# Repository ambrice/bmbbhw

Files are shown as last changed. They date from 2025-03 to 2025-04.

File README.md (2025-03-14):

# Big Mouth Billy Bass Master Control Program

This is the hardware design for the Big Mouth Billy Bass controller.  The current
software (zephyr version) runs on a group of 6 adafruit boards with a lot of
wires running between them.  So this is my first hardware design attempt, to use
the adafruit boards as a reference and compile them into one board.

The adafruit schematics are available under EAGLE which is a dead-end program, so
using KiCad 8 to design the board.  Started with brand-new KiCad 9, but it was
suggested that KiCad 8 would be more stable and have less potential issues with
manufacturing, Osh Park for example accepts KiCad 8 board files directly but not
KiCad 9 yet.

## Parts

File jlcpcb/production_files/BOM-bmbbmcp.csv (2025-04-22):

Comment | Designator | Footprint | LCSC | Quantity
220pF | C8,C9 | C_0805_2012Metric | C107145 | 2
DRV8835DSSR | U4 | DSS0012A | C129328 | 1
MBR120 | D1,D2 | D_SOD-123 | C130880 | 2
USB_OTG | J1 | USB_Micro-AB_Molex_47590-0001 | C136001 | 1
0.1uF | C11,C2,C5 | C_0603_1608Metric | C14663 | 3
10uF | C1,C10,C6,C7 | C_0805_2012Metric | C15850 | 4
22pF | C3,C4 | C_0603_1608Metric | C1653 | 2
22 | R2,R3 | R_0603_1608Metric | C23345 | 2
10k | R1 | R_0603_1608Metric | C25804 | 1
FerriteBead | FB1,FB2 | L_0805_2012Metric | C442498 | 2
AP2112K-3.3 | U2 | SOT-23-5 | C51118 | 1
MDBT50Q-P1MV2 | U1 | Raytac_MDBT50Q | C5119772 | 1
Micro_SD_Card | J4 | microSD_HC_Molex_104031-0811 | C585350 | 1
32.768 | Y1 | Crystal_SMD_MicroCrystal_CC7V-T1A-2Pin_3.2x1.5mm | C620155 | 1
MAX98357A | U3 | TQFN-16-1EP_3x3mm_P0.5mm_EP1.23x1.23mm | C910544 | 1
KMR231GLFS | S1,S2 | SW4SMD_63X161LS | C99271 | 2

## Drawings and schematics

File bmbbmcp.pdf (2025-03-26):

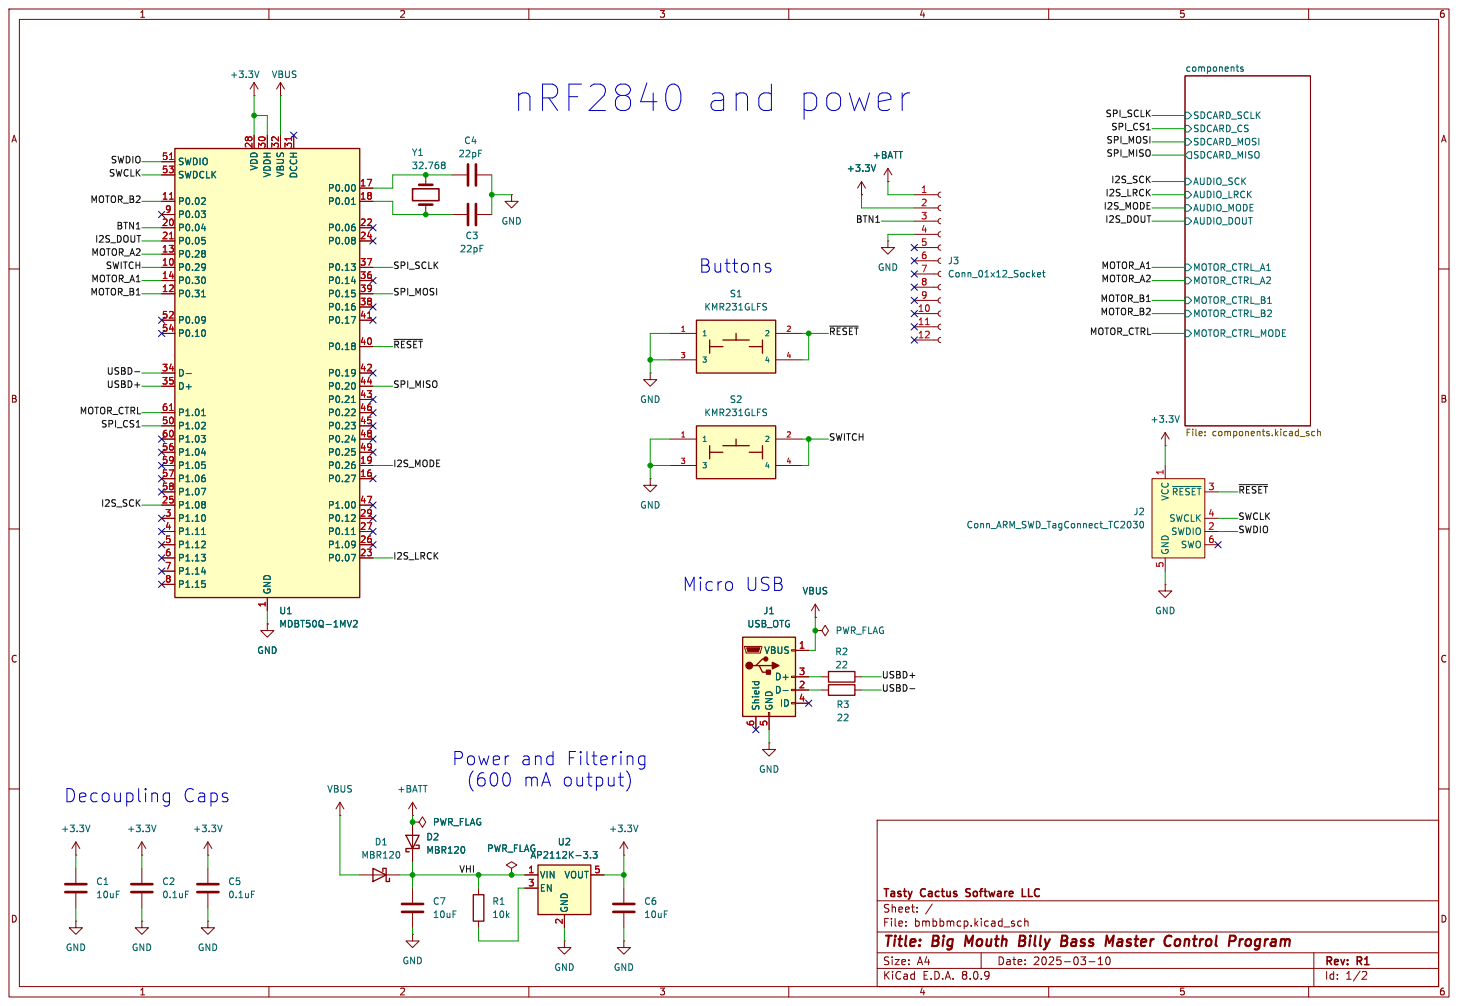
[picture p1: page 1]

1 P0.29 10 P0.02 11 P0.31 12 P0.28 13 P0.30 14 P0.27 16 P0.00 17 P0.01 18 P0.26 19 P0.04 20 P0.05 21 P0.06 22 P0.07 23 P0.08 24 P1.08 25 P1.09 26 P0.11 27 VDD 28 P0.12 29 P1.10 3 VDDH 30 DCCH 31 VBUS 32 D- 34 D+ 35 P0.14 36 P0.13 37 P0.16 38 P0.15 39 P1.11 4 P0.18 40 P0.17 41 P0.19 42 P0.21 43 P0.20 44 P0.23 45 P0.22 46 P1.00 47 P0.24 48 P0.25 49 P1.12 5 P1.02 50 SWDIO 51 P0.09 52 SWDCLK 53 P0.10 54 P1.04 56 P1.06 57 P1.07 58 P1.05 59 P1.13 6 P1.03 60 P1.01 61 P1.14 7 P1.15 8 P0.03 9 U1 MDBT50Q-1MV2 C1
SWDIO
SWCLK

1 P0.29 10 P0.02 11 P0.31 12 P0.28 13 P0.30 14 P0.27 16 P0.00 17 P0.01 18 P0.26 19 P0.04 20 P0.05 21 P0.06 22 P0.07 23 P0.08 24 P1.08 25 P1.09 26 P0.11 27 VDD 28 P0.12 29 P1.10 3 VDDH 30 DCCH 31 VBUS 32 D- 34 D+ 35 P0.14 36 P0.13 37 P0.16 38 P0.15 39 P1.11 4 P0.18 40 P0.17 41 P0.19 42 P0.21 43 P0.20 44 P0.23 45 P0.22 46 P1.00 47 P0.24 48 P0.25 49 P1.12 5 P1.02 50 SWDIO 51 P0.09 52 SWDCLK 53 P0.10 54 P1.04 56 P1.06 57 P1.07 58 P1.05 59 P1.13 6 P1.03 60 P1.01 61 P1.14 7 P1.15 8 P0.03 9 VBUS

1 SWDIO 2 ~{RESET}3 SWCLK 4 GND

Id: 1/2 Title: Big Mouth Billy Bass Master Control Program

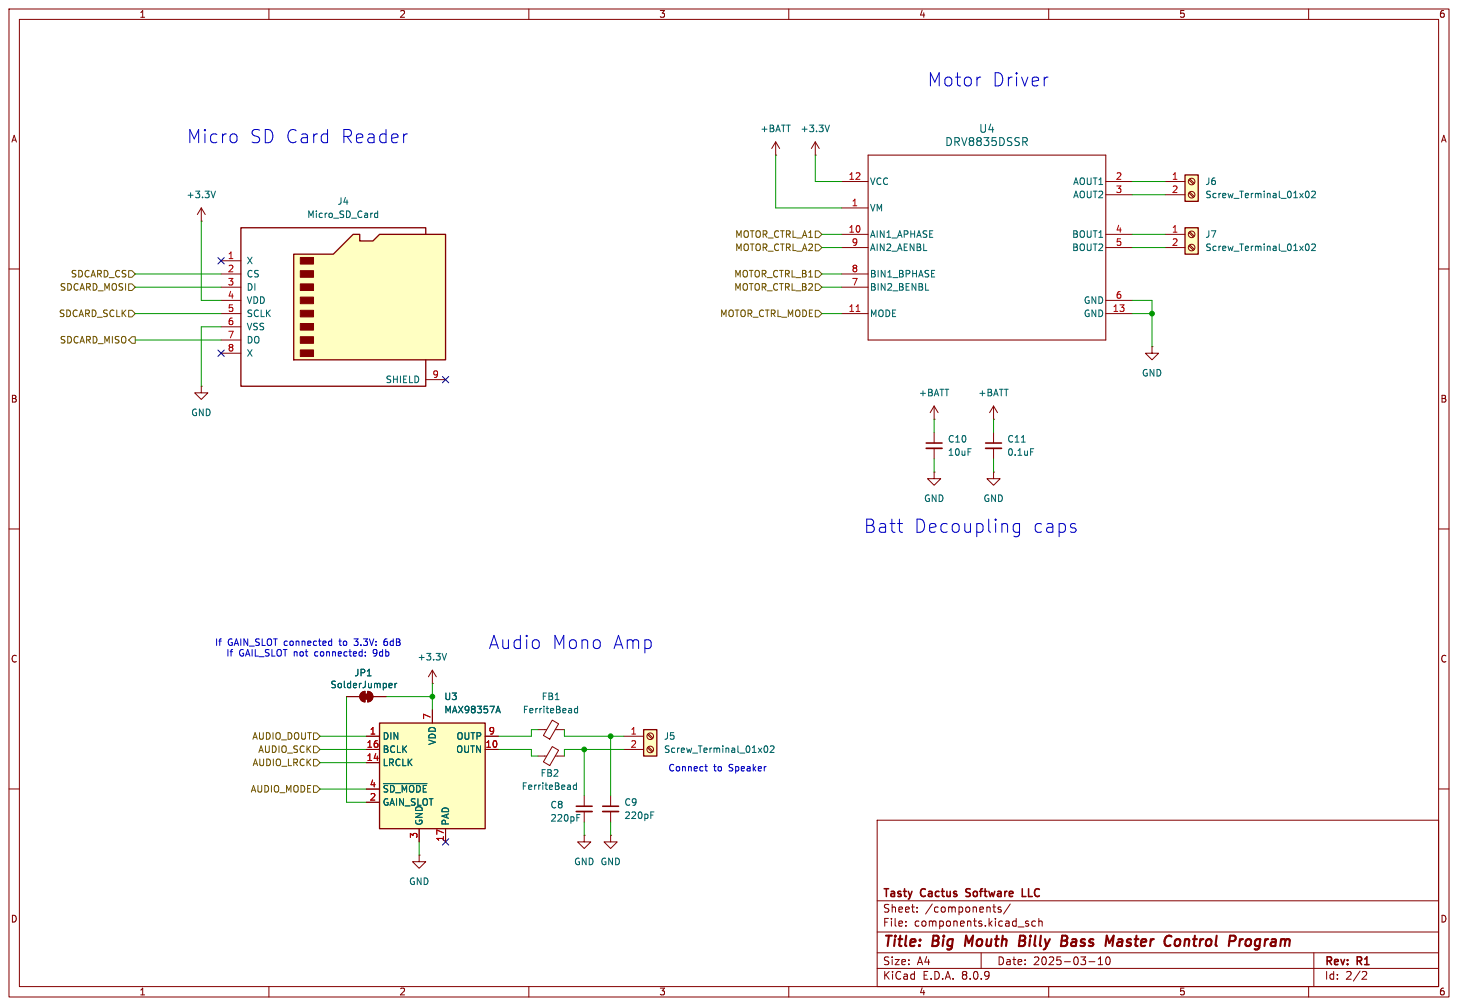
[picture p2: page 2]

File: components.kicad_sch Sheet: /components/
Id: 2/2 Title: Big Mouth Billy Bass Master Control Program

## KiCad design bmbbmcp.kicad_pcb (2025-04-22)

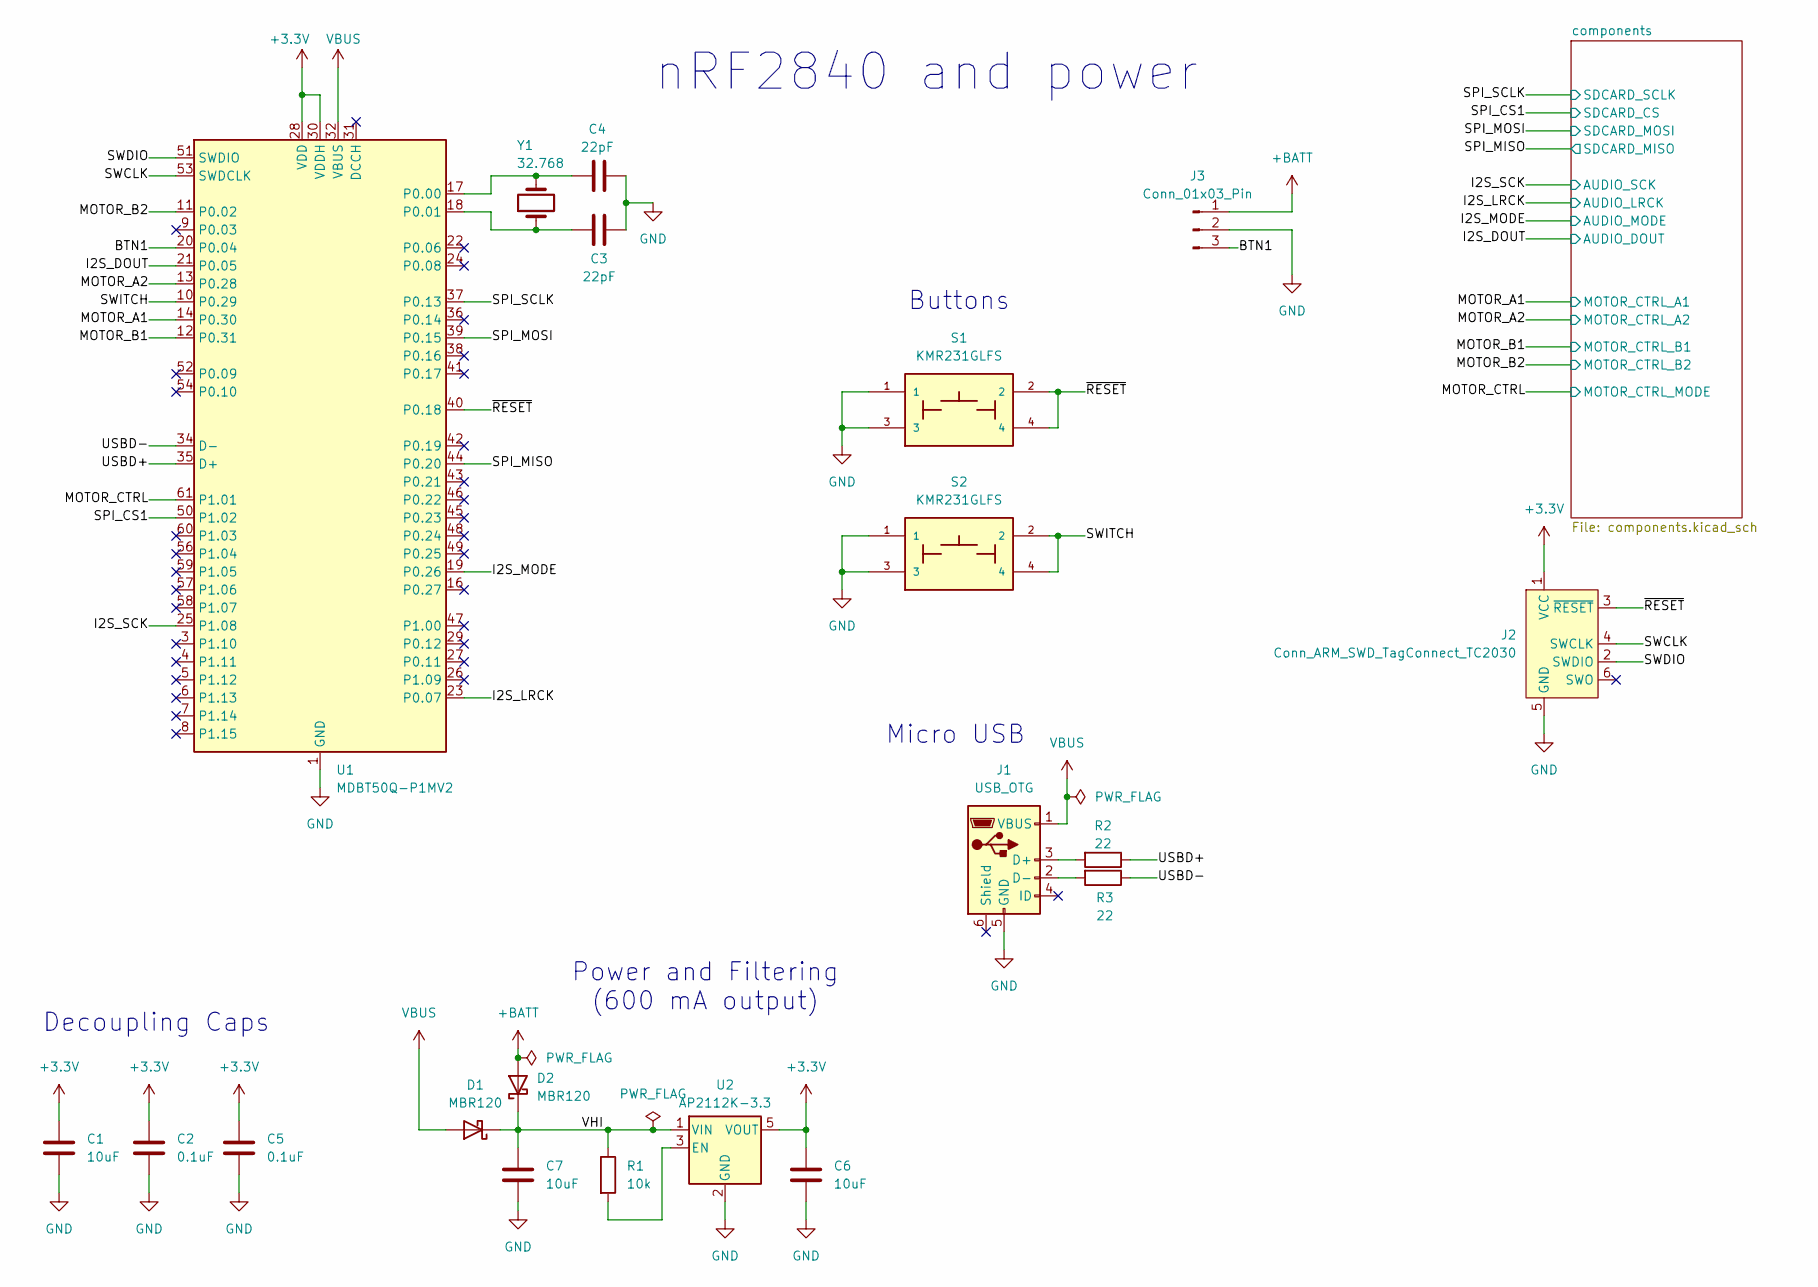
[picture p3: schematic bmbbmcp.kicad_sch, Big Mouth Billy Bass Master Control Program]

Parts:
C1, C6, C7: 10uF; C_0805_2012Metric; LCSC C15850
C2, C5: 0.1uF; C_0603_1608Metric; LCSC C14663
C3, C4: 22pF; C_0603_1608Metric; LCSC C1653
D1, D2: MBR120; D_SOD-123; LCSC C130880
J1: USB_OTG; USB_Micro-AB_Molex_47590-0001; LCSC C136001
J2: Conn_ARM_SWD_TagConnect_TC2030; Tag-Connect_TC2030-IDC-NL_2x03_P1.27mm_Vertical
J3: Conn_01x03_Pin; PinHeader_1x03_P2.54mm_Vertical
R1: 10k; R_0603_1608Metric; LCSC C25804
R2, R3: 22; R_0603_1608Metric; LCSC C23345
S1, S2: KMR231GLFS; SW4SMD_63X161LS; LCSC C99271
U1: MDBT50Q-P1MV2; Raytac_MDBT50Q; LCSC C5118826
U2: AP2112K-3.3; SOT-23-5; LCSC C51118
Y1: 32.768; Crystal_SMD_MicroCrystal_CC7V-T1A-2Pin_3.2x1.5mm; LCSC C620155

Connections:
+3.3V: C1.1, C2.1, C5.1, C6.1, J2.1 (VCC), U1.28 (VDD), U1.30 (VDDH), U2.5 (VOUT); also elsewhere on the board
+BATT: D2.2 (A), J3.1; also elsewhere on the board
/BTN1: J3.3, U1.20 (P0.04)
/I2S_DOUT: U1.21 (P0.05); also elsewhere on the board
/I2S_LRCK: U1.23 (P0.07); also elsewhere on the board
/I2S_MODE: U1.19 (P0.26); also elsewhere on the board
/I2S_SCK: U1.25 (P1.08); also elsewhere on the board
/MOTOR_A1: U1.14 (P0.30); also elsewhere on the board
/MOTOR_A2: U1.13 (P0.28); also elsewhere on the board
/MOTOR_B1: U1.12 (P0.31); also elsewhere on the board
/MOTOR_B2: U1.11 (P0.02); also elsewhere on the board
/MOTOR_CTRL: U1.61 (P1.01); also elsewhere on the board
/SPI_CS1: U1.50 (P1.02); also elsewhere on the board
/SPI_MISO: U1.44 (P0.20); also elsewhere on the board
/SPI_MOSI: U1.39 (P0.15); also elsewhere on the board
/SPI_SCLK: U1.37 (P0.13); also elsewhere on the board
/SWCLK: J2.4 (SWCLK), U1.53 (SWDCLK)
/SWDIO: J2.2 (SWDIO), U1.51 (SWDIO)
/SWITCH: S2.2, S2.4, U1.10 (P0.29)
/USBD+: R2.1, U1.35 (D+)
/USBD-: R3.1, U1.34 (D-)
/VHI: C7.1, D1.1 (K), D2.1 (K), R1.1, U2.1 (VIN)
/~RESET: J2.3 (~RESET), S1.2, S1.4, U1.40 (P0.18)
GND: C1.2, C2.2, C3.1, C4.1, C5.2, C6.2, C7.2, J1.5 (GND), J2.5 (GND), J3.2, S1.1, S1.3, S2.1, S2.3, U1.1 (GND), U1.2 (GND), U1.15 (GND), U1.33 (GND), U1.55 (GND), U2.2 (GND); also elsewhere on the board
unnamed: J1.3 (D+), R2.2
unnamed: J1.2 (D-), R3.2
unnamed: C4.2, U1.17 (P0.00), Y1.2
unnamed: C3.2, U1.18 (P0.01), Y1.1
unnamed: R1.2, U2.3 (EN)
VBUS: D1.2 (A), J1.1 (VBUS), U1.32 (VBUS)

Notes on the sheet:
Micro USB
Buttons
nRF2840 and power
Decoupling Caps
Power and Filtering (600 mA output)

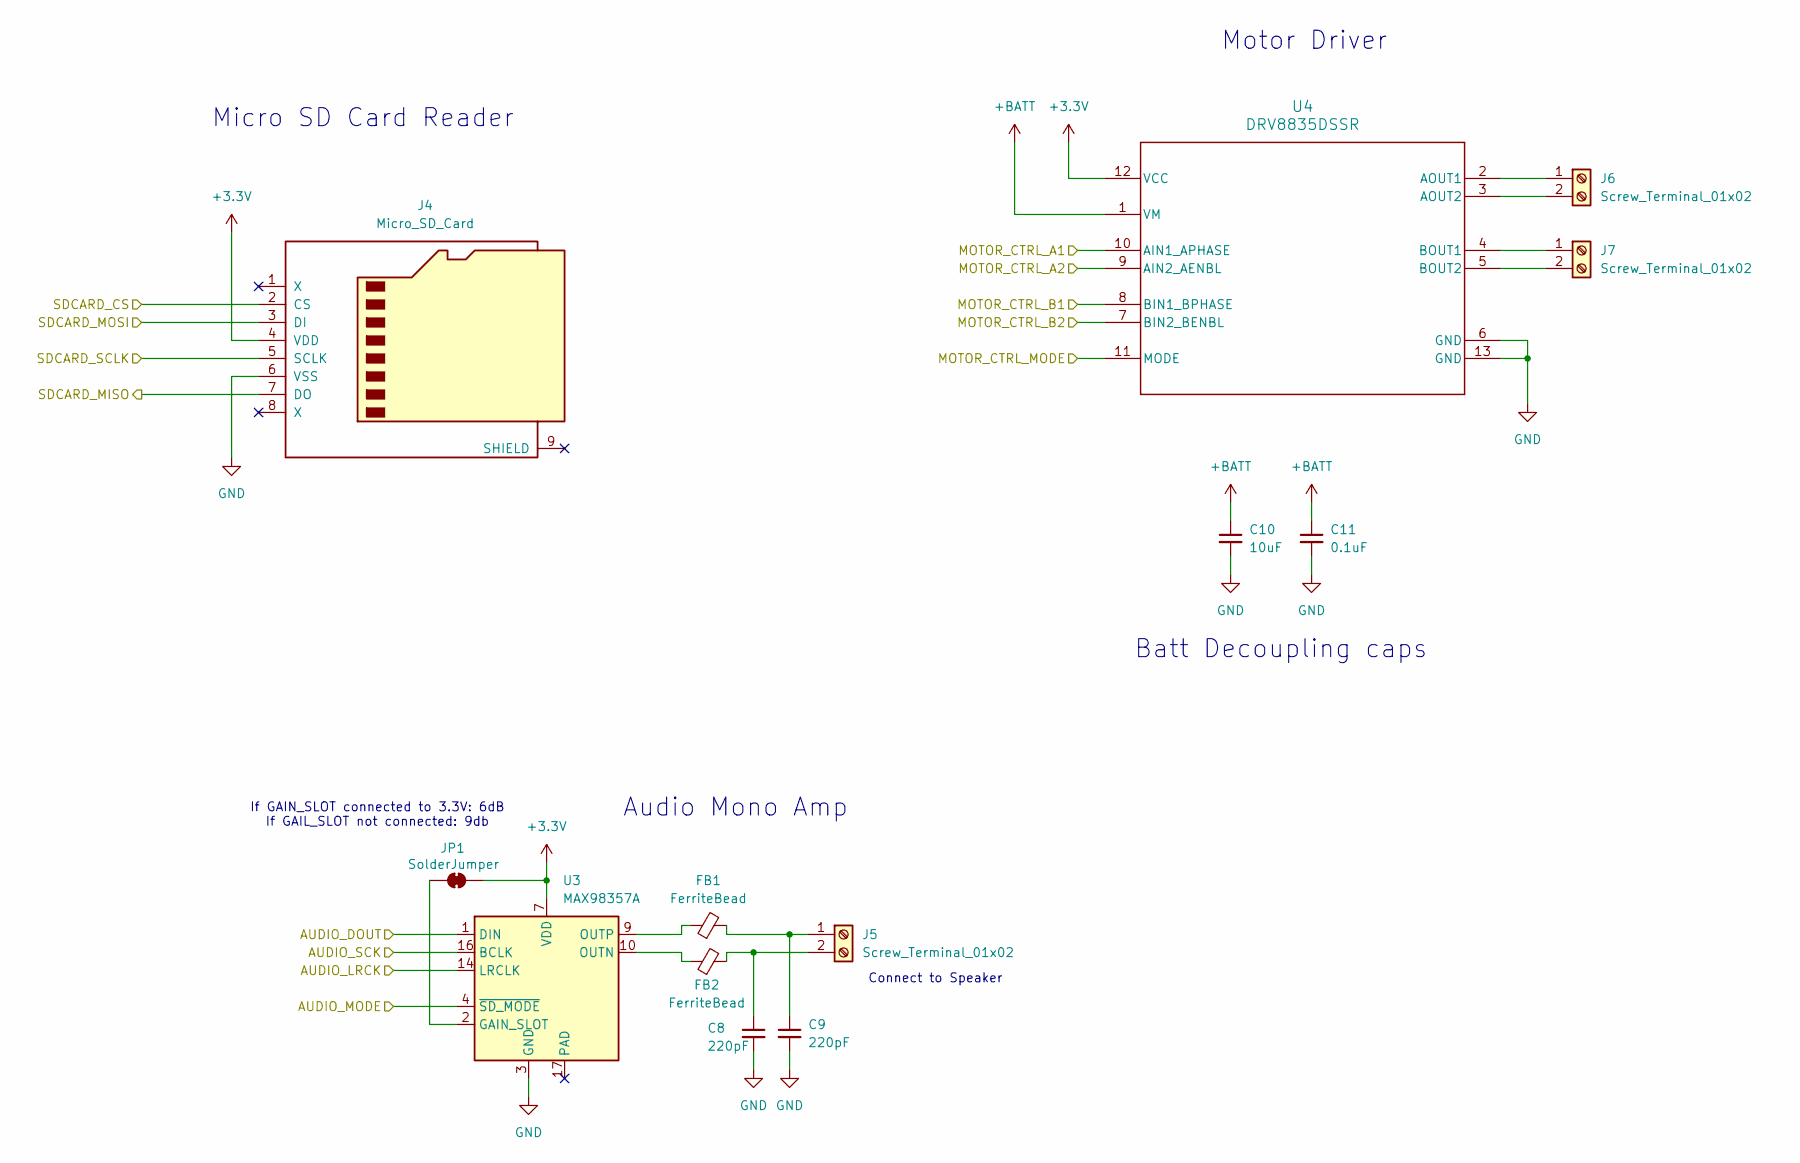
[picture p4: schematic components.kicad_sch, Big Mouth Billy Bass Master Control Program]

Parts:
C8, C9: 220pF; C_0805_2012Metric
C10: 10uF; C_0805_2012Metric
C11: 0.1uF; C_0603_1608Metric
FB1, FB2: FerriteBead; L_0805_2012Metric
J4: Micro_SD_Card; microSD_HC_Molex_104031-0811
J5, J6, J7: Screw_Terminal_01x02; TerminalBlock_MetzConnect_Type059_RT06302HBWC_1x02_P3.50mm_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
JP1: SolderJumper; SolderJumper-2_P1.3mm_Bridged_RoundedPad1.0x1.5mm
U3: MAX98357A; TQFN-16-1EP_3x3mm_P0.5mm_EP1.23x1.23mm
U4: DRV8835DSSR; DSS0012A

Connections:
+3.3V: J4.4 (VDD), JP1.2 (B), U3.7 (VDD), U3.8 (VDD), U4.12 (VCC); also elsewhere on the board
+BATT: C10.1, C11.1, U4.1 (VM); also elsewhere on the board
/I2S_DOUT: U3.1 (DIN); also elsewhere on the board
/I2S_LRCK: U3.14 (LRCLK); also elsewhere on the board
/I2S_MODE: U3.4 (~SD_MODE); also elsewhere on the board
/I2S_SCK: U3.16 (BCLK); also elsewhere on the board
/MOTOR_A1: U4.10 (AIN1_APHASE); also elsewhere on the board
/MOTOR_A2: U4.9 (AIN2_AENBL); also elsewhere on the board
/MOTOR_B1: U4.8 (BIN1_BPHASE); also elsewhere on the board
/MOTOR_B2: U4.7 (BIN2_BENBL); also elsewhere on the board
/MOTOR_CTRL: U4.11 (MODE); also elsewhere on the board
/SPI_CS1: J4.2 (CS); also elsewhere on the board
/SPI_MISO: J4.7 (DO); also elsewhere on the board
/SPI_MOSI: J4.3 (DI); also elsewhere on the board
/SPI_SCLK: J4.5 (SCLK); also elsewhere on the board
GND: C8.2, C9.2, C10.2, C11.2, J4.6 (VSS), U3.3 (GND), U3.11 (GND), U3.15 (GND), U4.6 (GND), U4.13 (GND), U4.V; also elsewhere on the board
unnamed: C9.1, FB1.2, J5.1
unnamed: C8.1, FB2.2, J5.2
unnamed: J6.1, U4.2 (AOUT1)
unnamed: J6.2, U4.3 (AOUT2)
unnamed: J7.1, U4.4 (BOUT1)
unnamed: J7.2, U4.5 (BOUT2)
unnamed: JP1.1 (A), U3.2 (GAIN_SLOT)
unnamed: FB2.1, U3.10 (OUTN)
unnamed: FB1.1, U3.9 (OUTP)

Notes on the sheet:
Connect to Speaker
Micro SD Card Reader
Audio Mono Amp
Motor Driver
Batt Decoupling caps
If GAIN_SLOT connected to 3.3V: 6dB If GAIL_SLOT not connected: 9db

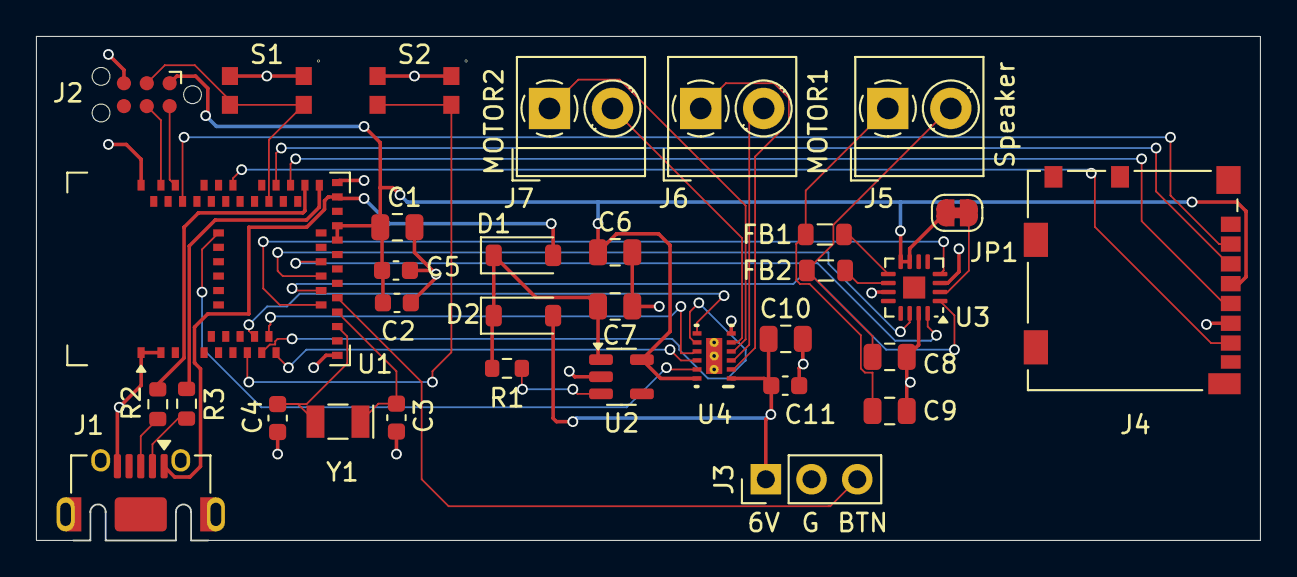
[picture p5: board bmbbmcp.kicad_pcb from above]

Board: 4 copper layers, 68.0 x 28.0 mm, 33 parts (0 on the bottom side), 39 nets.

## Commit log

2025-03-14 Schematic updates
    [BMBBHW.kicad_sch]
2025-03-14 Moving from KiCad 9.0 to 8.0.9
    KiCad 9 is very new and it was suggested that I should use stable KiCad 8 instead
    [BMBBHW.kicad_pcb, BMBBHW.kicad_sch, bmbbmcp.kicad_pcb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]
2025-03-19 Updated with routing, passes almost all design rule checks
    [bmbbmcp.kicad_pcb]
2025-03-20 Adding parts and gerber files from JLCPCB plugin
    [BOM-bmbbmcp.csv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]
2025-03-26 Initial full board design
    [BOM-bmbbmcp.csv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]
2025-04-21 Switch to three pin
    [bmbbmcp-CuBottom.gbr, bmbbmcp-CuIn1.gbr, bmbbmcp-CuIn2.gbr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]
2025-04-22 Switch MCU from MDBT50Q-1MV2 to MDBT50Q-P1MV2 (PCB antenna version, in stock)
    [BOM-bmbbmcp.csv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]
